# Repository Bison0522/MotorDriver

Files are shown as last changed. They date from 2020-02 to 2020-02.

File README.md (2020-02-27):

# MotorDriver

必ずマザーに220μF以上のコンデンサを一つ以上取り付けること．このコンデンサをつけなかったことで燃えた場合，その原因はモータによる逆起電圧がFETの定格電圧を超えたことであり，たいていはFETとTLPをすべて取り換えることで直すことができる．ただし，モータの電源でなくロジックの12Vに何らかのノイズが乗ったと思われる場合（モータとロジックの電源が共通であったなど）はこの限りではなく，ブートストラップ用（FETと同じ面に2つ実装．裏面の大きい4つのダイオードではない）のダイオードなどが故障している可能性がある．余裕があれば新しいものを使用するべきである．

i2cアドレスは，DIPスイッチの#1が最下位ビットである．よって#1=on,#2=off,#3=off,#4=offであれば0b0001000=0x08である．
Nucleoの場合，7bitのi2cアドレスに加え，最下位にRWビット（モータードライバはWrite限定のため0）を追加し8bit=1byteとして設定する必要があるため，0x10がこの時のスレーブアドレスとなる．

GMDB2-Dは単体，E-ASSEMBLEが発注用に面付したもの．E.zipを発注すればよい．名前が違うのは，Eにする際にDに上書きしたので名前がそのままなだけで深い意味はない．

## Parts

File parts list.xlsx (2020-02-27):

緑色チップＬＥＤ ［１６０８］ ＯＳＴＧ１６０８Ｃ１Ａ （２０個入） (http://akizukidenshi.com/catalog/g/gI-06417/)
青色チップＬＥＤ ［１６０８］ ＯＳＢＬ１６０８ （２０個入） (http://akizukidenshi.com/catalog/g/gI-03982/)
黄色チップＬＥＤ ［１６０８］ ＯＳＹＬ１６０８ （２０個入） (http://akizukidenshi.com/catalog/g/gI-03984/)
赤色チップＬＥＤ ［１６０８］ ＯＳＨＲ１６０８ （２０個入） (http://akizukidenshi.com/catalog/g/gI-03978/)
表面実装用ＵＳＢコネクタ ｍｉｃｒｏＢメス 標準タイプ（ボトムマウント） （５個入） (http://akizukidenshi.com/catalog/g/gC-11183/)
表面実装用ショットキーバリアダイオード（４０Ｖ２Ａ）ＳＳ２０４０ＦＬ（２０個入） (http://akizukidenshi.com/catalog/g/gI-02073/)
チップ積層セラミックコンデンサー ２２μＦ２５Ｖ Ｘ５Ｒ ２０１２ （１０個入） (http://akizukidenshi.com/catalog/g/gP-08240/)
表面実装用タクトスイッチ ２．５５Ｎ ＳＫＲＰＡＣＥ０１０ （５個入） (http://akizukidenshi.com/catalog/g/gP-06185/)
チップ積層セラミックコンデンサー １５ｐＦ５０Ｖ ＮＰ０ １６０８ （４０個入） (http://akizukidenshi.com/catalog/g/gP-13312/)
表面実装型クリスタル（水晶発振子） １２ＭＨｚ （４個入） (http://akizukidenshi.com/catalog/g/gP-05225/)
ＰＩＣマイコンＰＩＣ１８Ｆ１４Ｋ５０Ｔ－Ｉ／ＳＳ（ＵＳＢ内蔵） (http://akizukidenshi.com/catalog/g/gI-04437/)
２回路ＡＮＤ ＴＣ７ＷＺ０８ＦＫ (http://akizukidenshi.com/catalog/g/gI-10799/)
フォトカプラ ＧａＡｌＡｓ赤外ＬＥＤ＋フォトＩＣ ＴＬＰ１５２ (http://akizukidenshi.com/catalog/g/gI-10824/)
２回路２入力ＯＲゲート ＴＣ７Ｗ３２ＦＵ （５個入） (http://akizukidenshi.com/catalog/g/gI-10466/)
表面実装ＤＩＰスイッチ ４Ｐ (http://akizukidenshi.com/catalog/g/gP-08929/)
https://www.mouser.com/ProductDetail/STMicroelectronics/STL180N6F7

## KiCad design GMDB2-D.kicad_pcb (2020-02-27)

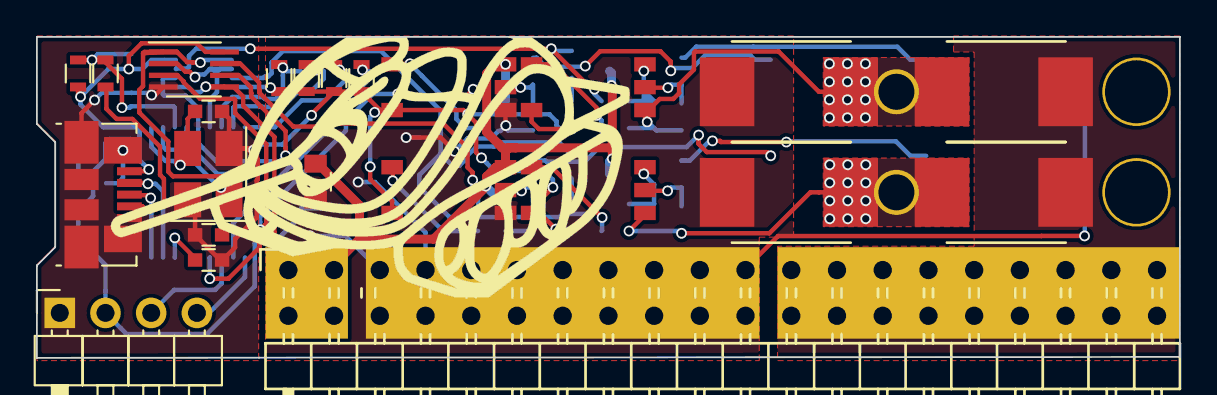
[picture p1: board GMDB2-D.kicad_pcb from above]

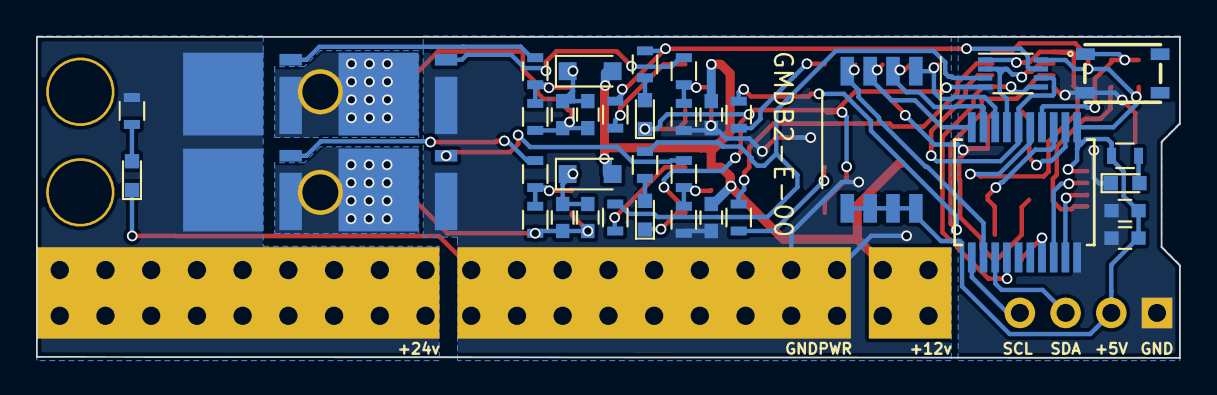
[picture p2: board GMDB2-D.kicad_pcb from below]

Board: 2 copper layers, 63.5 x 17.8 mm, 63 parts (38 on the bottom side), 46 nets.

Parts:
C1, C3, C4, C5, C6, C8, C9, C10: 0.1u; C_0603
C2: 1u; C_0603
C7: 22u; C_0805
C11, C12: C; C_0603
D1, D2, D3, D7: LED; LED_0603
D4, D10: SBD; D_SOD-323_HandSoldering
D5, D6, D8, D9: SBD; SKB-SK54
J1: USB_Micro; USB_Micro-B_Molex_47346-0001
J2: I2C; PIN4
J4: POWER; Pin_Header_Angled_2x20
Q1, Q2, Q3, Q4: NchFET; STL120N8F7
R1: JP; R_0603
R2, R3, R4, R5, R6, R12, R13, R19, R20: 10k; R_0603
R7, R8, R9, R10, R11, R21, R22: 510; R_0603
R14, R15, R17, R18: 47; R_0603
R16: 4.7k; R_0603
S1: SKRPACE010; tactsw
SW1: ADDRESS; dipsw
U1: PIC18F14K50-I/SS; PIC18F14K50
U2: AND2; VSSOP-8_2.3x2mm_Pitch0.5mm
U3, U4, U5, U6: TLP152
U7: OR2; SSOP-8_2.95x2.8mm_Pitch0.65mm
Y1: Crystal_GND24; Crystal_SMD_EuroQuartz_MT-4pin_3.2x2.5mm_HandSoldering
hoge: HOLE
via: v; via

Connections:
*MCLR: R1.1, R6.2, S1.1, U1.4
+5V: C1.1, C2.1, J1.1, J2.2, R6.1, R7.1, SW1.5, SW1.6, SW1.7, SW1.8, U1.1, U2.8, U7.8
+12V: C5.1, C7.1, C10.1, D4.2, D10.2, J4.1, U4.6, U6.6
+24V: D5.1, D8.1, J4.3, Q1.1, Q3.1, R16.1
CCW: U1.14, U2.5, U7.5
CW: U1.7, U2.2, U7.2
GND: C1.2, C2.2, C3.1, C11.1, C12.2, D1.1, D2.1, D3.1, J1.5, J1.6, J2.1, R2.2, R3.2, R4.2, R5.2, S1.3, U1.20, U2.4, U3.3, U4.3, U5.3, U6.3, U7.4, Y1.2, Y1.4
GNDPWR: C5.2, C7.2, C10.2, D6.2, D7.1, D9.2, J4.2, Q2.3, Q4.3, R13.2, R20.2, U4.4, U6.4
unnamed: C3.2, U1.17
unnamed: C4.1, C6.1, D4.1, U3.6
unnamed: C4.2, C6.2, D5.2, D6.1, Q1.3, Q2.1, R12.2, U3.4, hoge.1
unnamed: C8.1, C9.1, D10.1, U5.6
unnamed: C8.2, C9.2, D8.2, D9.1, Q3.3, Q4.1, R19.2, U5.4
unnamed: C11.2, U1.3, Y1.1
unnamed: C12.1, U1.2, Y1.3
unnamed: D1.2, R7.2
unnamed: D2.2, R10.2
unnamed: D3.2, R11.2
unnamed: D7.2, R16.2
unnamed: J1.4, R1.2
unnamed: Q1.2, R14.1
unnamed: Q2.2, R15.1
unnamed: Q3.2, R17.1
unnamed: Q4.2, R18.1
unnamed: R2.1, SW1.3, U1.10
unnamed: R3.1, SW1.2, U1.9
unnamed: R4.1, SW1.1, U1.8
unnamed: R5.1, SW1.4, U1.12
unnamed: R8.1, U3.1
unnamed: R9.1, U4.1
unnamed: R12.1, R14.2, U3.5
unnamed: R13.1, R15.2, U4.5
unnamed: R17.2, R19.1, U5.5
unnamed: R18.2, R20.1, U6.5
unnamed: R21.1, U5.1
unnamed: R22.1, U6.1
PGC/D-: J1.2, U1.18
PGD/D+: J1.3, U1.19
PWM-A: U1.5, U2.1, U7.1
PWM-A-AND: R8.2, R10.1, U2.7
PWM-A-OR: R22.2, U7.7
PWM-B: U1.6, U2.6, U7.6
PWM-B-AND: R11.1, R21.2, U2.3
PWM-B-OR: R9.2, U7.3
SCL: J2.4, U1.11
SDA: J2.3, U1.13

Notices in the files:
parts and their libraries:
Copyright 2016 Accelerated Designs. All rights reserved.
